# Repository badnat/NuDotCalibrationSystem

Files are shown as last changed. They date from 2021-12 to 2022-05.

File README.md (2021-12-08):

# NuDotCalibrationSystem

This project is for the NuDot Experiment https://jgruszko.web.unc.edu/experiments/. I am a student at UNC who will be graduating in May 2022. I am working with Dr. Gruszko to develop the code and electronics to control the calibration system for the NuDot experiment. The goal of this experiment is to detect neutrinoless double beta decay. Neutrinoless double beta decay is a very rare phenomenon. Because of this, it is difficult to distinguish signal from background during detection. NuDots goal is to reduce the background by detecting cherenkov radiation from single electron events produced by background events as opposed to the double electrons given off by double beta decay. 
 
The goal of my code and electronics is to move a point beta ray source to an exact height, inclination, and rotation. Knowing these allows NuDot to calibrate the precise timings given by the detectors. These timings are extremely important for event building, where we determine details about the event causing the signal such as the position and energy. 

## My Approach and Method
Having previously taken a class full dedicated to working with microcontrollers, my first thought for this project was to use a Raspberry Pi. I ruled out Arduinos because I needed a file system to save multiple files and wanted the flexibility of a microcontroller with an OS for testing purposes. The problem ultimately boils down to moving 3 stepper motors into position, verifying the accuracy of that position, and recording that position for and future movements of the stepper. 
 
I achieved these objectives by using python code to control the stepper motors and a c++ program to read the data from the stepper encoders, interpret the data, and store the position in a file. The python code will only move the stepper and the c++ code will only determine its position. This allows me to independently verify the positions of the steppers and compensate for any step skipping that might occur. This ensures that we always accurately know the positions of the steppers which is important for both calibration and mechanical reasons. Obviously we need to accurately know the position of the beta source to calibrate the system, but there are also a few mechanical hard stops that the steppers would be unable to push past (blocked by a lot of metal). I could have used a sensor to determine the position in space but decided to make my code very robust to avoid the issue all together. 

#### Code Structure
I decided on an object oriented approach for ease of use and abstraction. The [Calibrator](https://github.com/badnat/NuDotCalibrationSystem/blob/main/calibrator.py) object is primarily for abstraction and handling error handling/edge cases. It holds all of the [Stepper](https://github.com/badnat/NuDotCalibrationSystem/blob/main/stepper.py) objects which send the signals to the stepper motors to move them. The [Stepper](https://github.com/badnat/NuDotCalibrationSystem/blob/main/stepper.py) objects also use bash commands to start up the [encoder](https://github.com/badnat/NuDotCalibrationSystem/blob/main/encoder.cpp) code for that stepper motor. 

## Assembled Calibration System
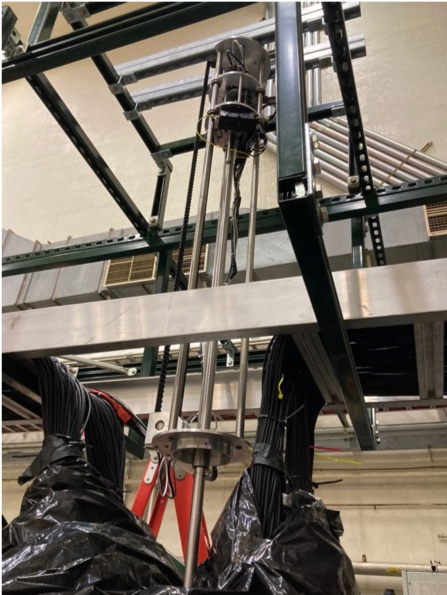
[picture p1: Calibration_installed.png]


## Challenges and Future Improvements
- Fully implementation of code and handling a few more edge cases (almost finished)
- Implement code for the Daq system to control the Rpi remotely using ssh keys
- Finalize Electronics using a custom PCB and CAT6 cable to send signals to the steppers and to the Pi from the encoders

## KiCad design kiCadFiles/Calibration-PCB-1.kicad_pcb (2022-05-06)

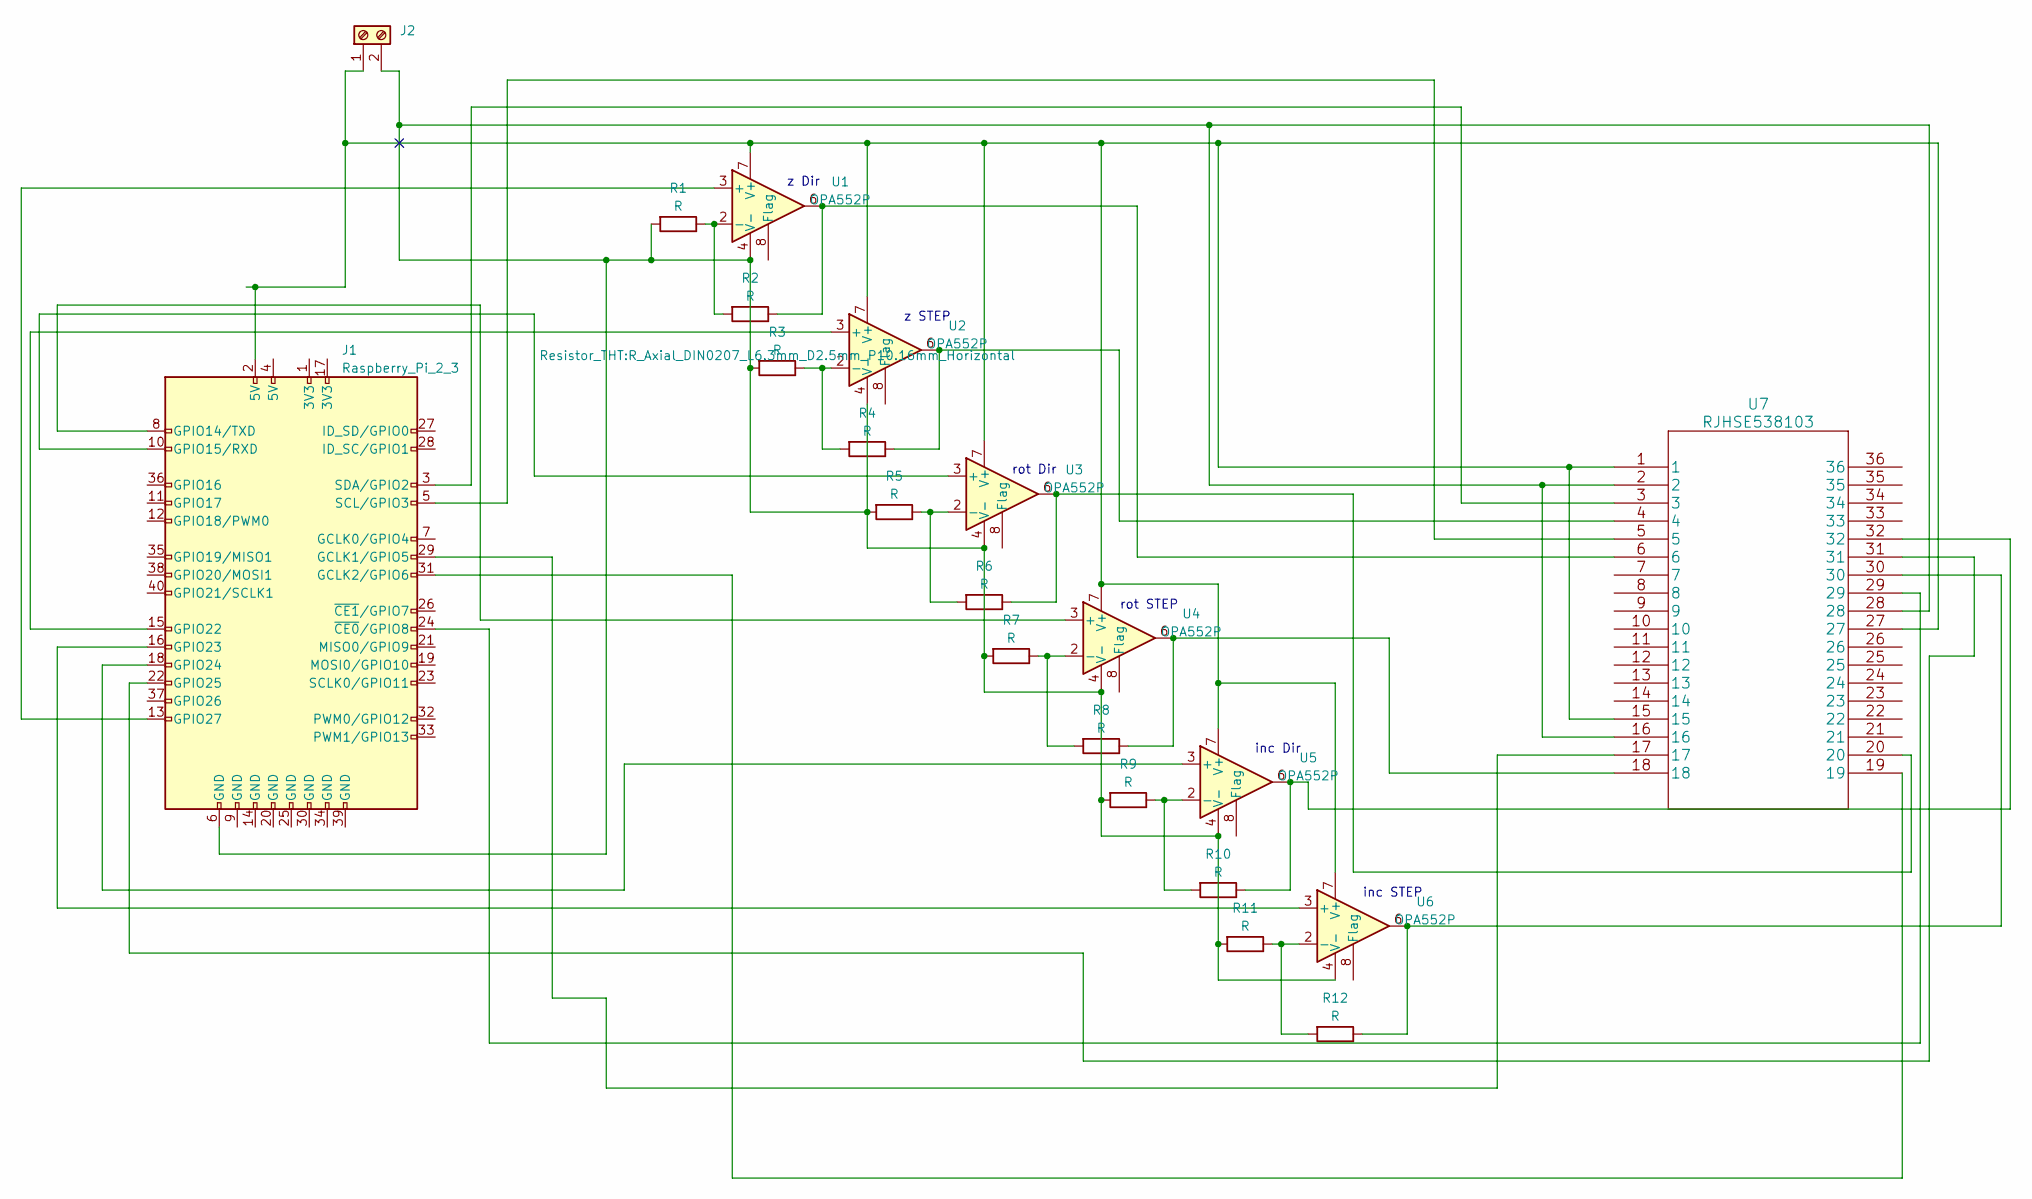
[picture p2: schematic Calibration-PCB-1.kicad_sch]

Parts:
J1: Raspberry_Pi_2_3; PinHeader_2x20_P2.54mm_Vertical
J2: (no value)
R1, R2, R3, R4, R5, R6, R7, R8, R9, R10, R11, R12: R; R_Axial_DIN0207_L6.3mm_D2.5mm_P10.16mm_Horizontal
U1, U2, U3, U4, U5, U6: OPA552P; DIP-8_W7.62mm
U7: RJHSE538103

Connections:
unnamed: J1.2 (5V), J2.1, U1.7 (V+), U2.7 (V+), U3.7 (V+), U4.7 (V+), U5.7 (V+), U6.7 (V+), U7.1, U7.15, U7.27
unnamed: J1.29 (GCLK1/GPIO5), U7.17
unnamed: J1.31 (GCLK2/GPIO6), U7.19
unnamed: J1.6 (GND), J2.2, R1.2, R3.2, R5.2, R7.2, R9.2, R11.2, U1.4 (V-), U2.4 (V-), U3.4 (V-), U4.4 (V-), U5.4 (V-), U6.4 (V-), U7.2, U7.16, U7.28
unnamed: J1.13 (GPIO27), U1.3 (+)
unnamed: J1.5 (SCL/GPIO3), U7.5
unnamed: J1.3 (SDA/GPIO2), U7.3
unnamed: R2.1, U1.6, U7.6
unnamed: R4.1, U2.6, U7.4
unnamed: R6.1, U3.6, U7.20
unnamed: R8.1, U4.6, U7.18
unnamed: R1.1, R2.2, U1.2 (-)
unnamed: J1.15 (GPIO22), U2.3 (+)
unnamed: R3.1, R4.2, U2.2 (-)
unnamed: J1.10 (GPIO15/RXD), U3.3 (+)
unnamed: R5.1, R6.2, U3.2 (-)
unnamed: J1.8 (GPIO14/TXD), U4.3 (+)
unnamed: R7.1, R8.2, U4.2 (-)
unnamed: J1.18 (GPIO24), U5.3 (+)
unnamed: R9.1, R10.2, U5.2 (-)
unnamed: J1.16 (GPIO23), U6.3 (+)
unnamed: R11.1, R12.2, U6.2 (-)
unnamed: J1.24 (~CE0/GPIO8), U7.29
unnamed: R12.1, U6.6, U7.30
unnamed: J1.22 (GPIO25), U7.31
unnamed: R10.1, U5.6, U7.32

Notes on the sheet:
rot STEP
rot Dir
z STEP
inc Dir
inc STEP
z Dir

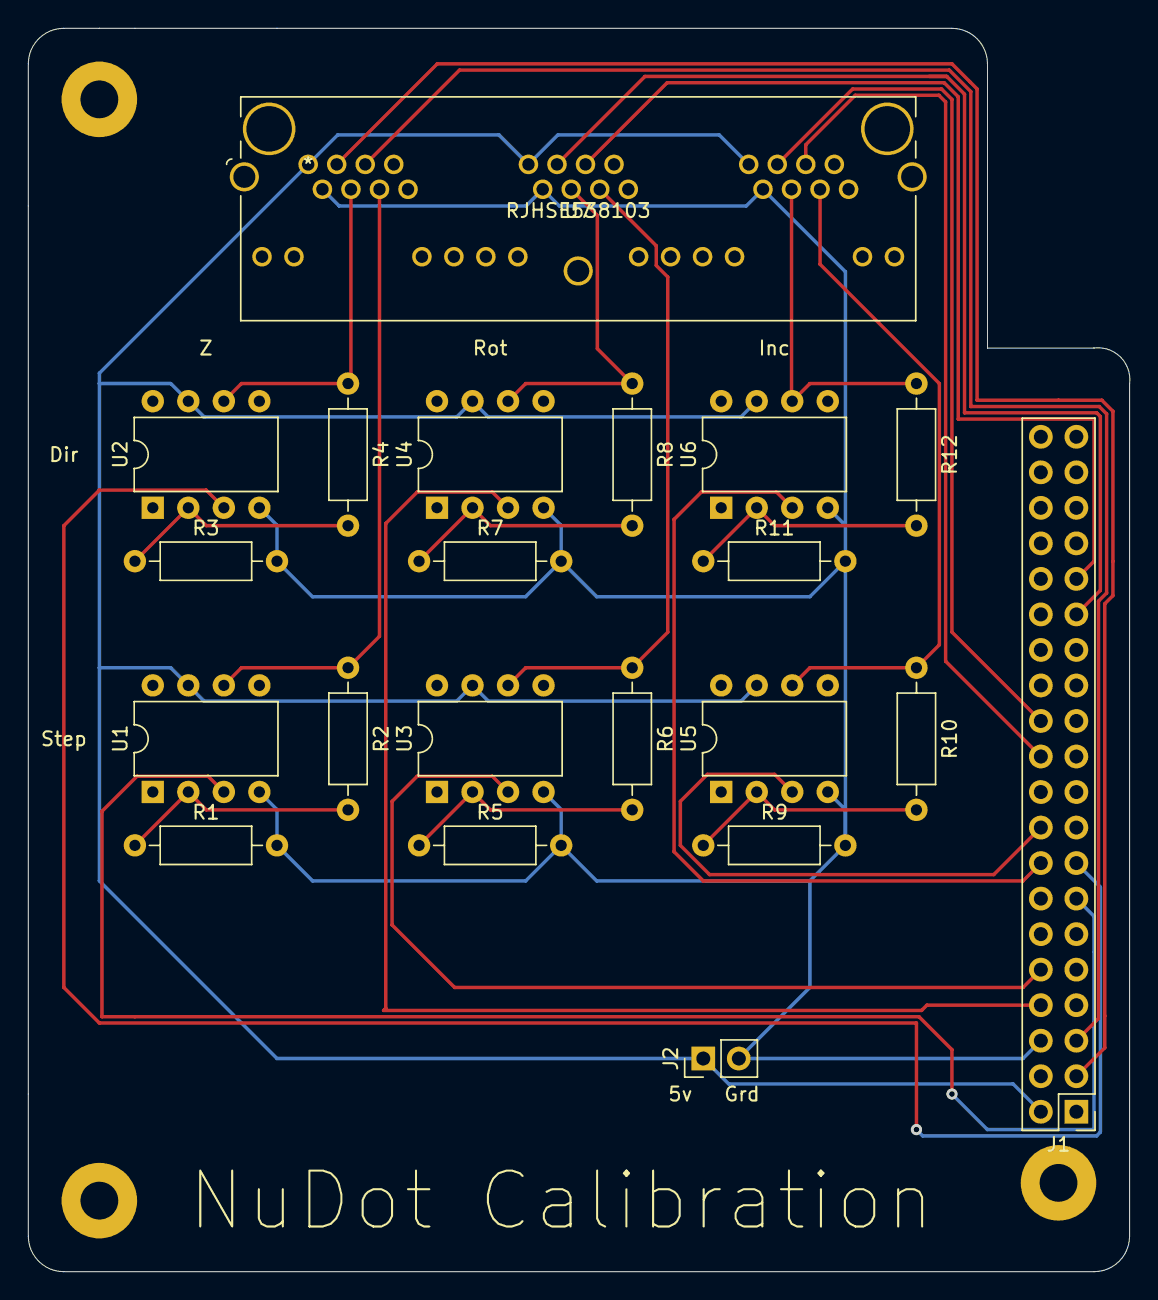
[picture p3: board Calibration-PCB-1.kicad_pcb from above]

Board: 2 copper layers, 78.8 x 88.9 mm, 21 parts (0 on the bottom side), 26 nets.

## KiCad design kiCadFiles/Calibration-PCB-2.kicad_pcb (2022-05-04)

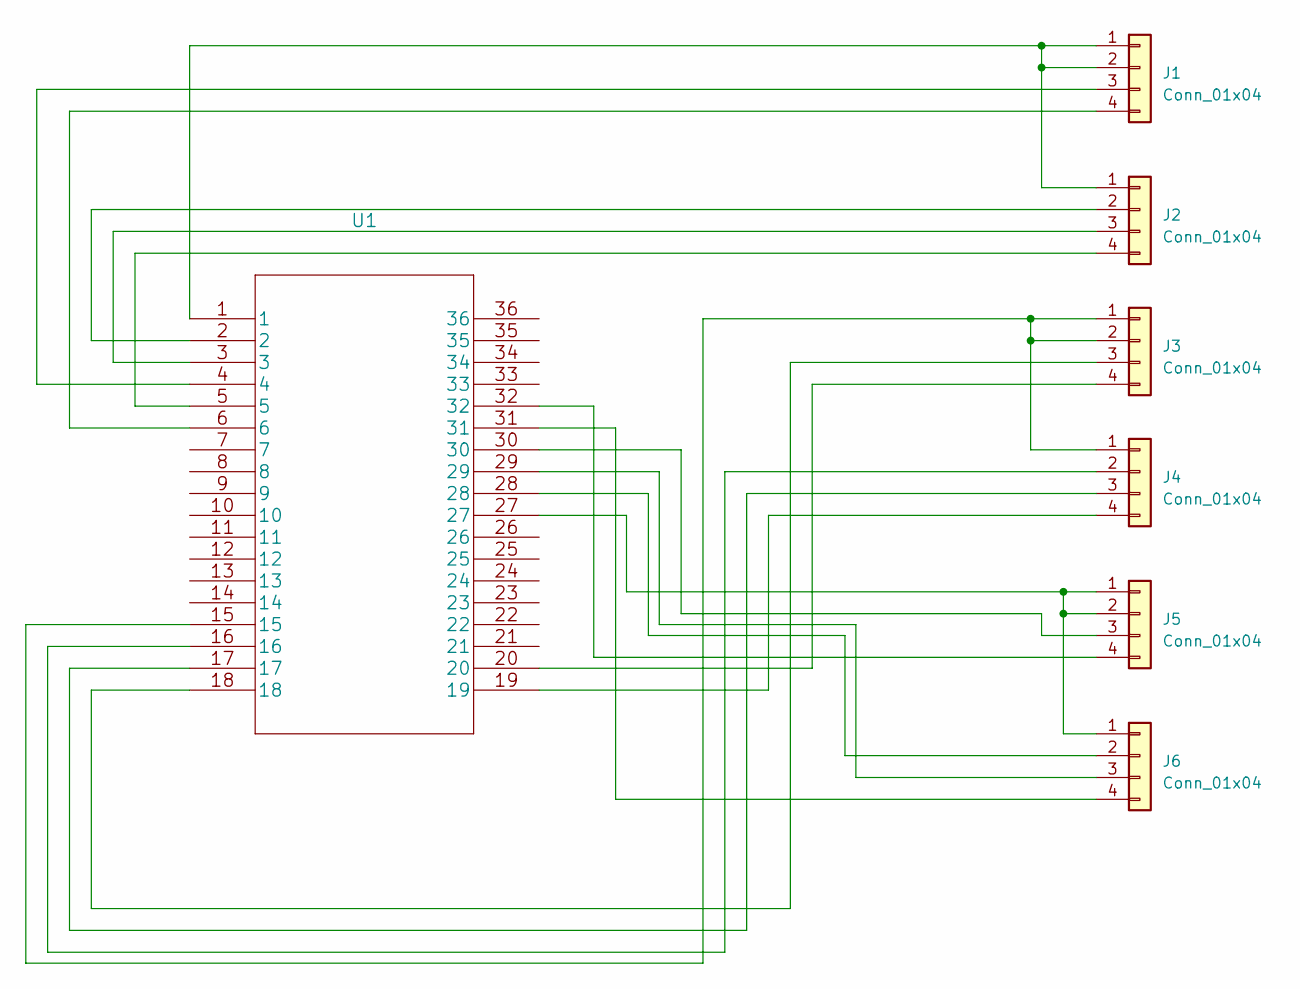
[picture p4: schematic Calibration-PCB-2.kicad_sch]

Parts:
J1, J2, J3, J4, J5, J6: Conn_01x04; PinSocket_1x04_P2.54mm_Vertical
U1: (no value)

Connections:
unnamed: J1.1, J1.2, J2.1, U1.1
unnamed: J1.3, U1.4
unnamed: J1.4, U1.6
unnamed: J2.2, U1.2
unnamed: J2.3, U1.3
unnamed: J2.4, U1.5
unnamed: J3.1, J3.2, J4.1, U1.15
unnamed: J3.3, U1.18
unnamed: J3.4, U1.20
unnamed: J4.2, U1.16
unnamed: J4.3, U1.17
unnamed: J4.4, U1.19
unnamed: J5.1, J5.2, J6.1, U1.27
unnamed: J5.3, U1.30
unnamed: J5.4, U1.32
unnamed: J6.2, U1.28
unnamed: J6.3, U1.29
unnamed: J6.4, U1.31

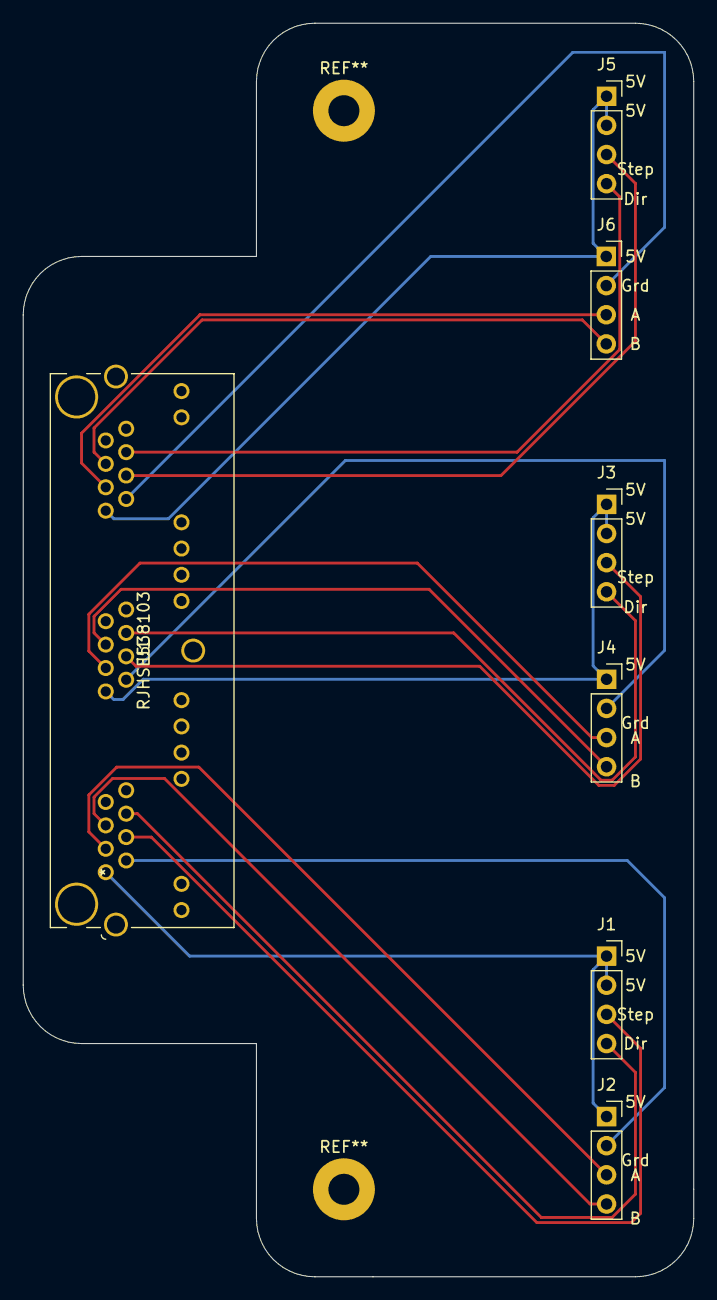
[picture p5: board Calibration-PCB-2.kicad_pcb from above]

Board: 2 copper layers, 58.4 x 109.2 mm, 7 parts (0 on the bottom side), 18 nets.

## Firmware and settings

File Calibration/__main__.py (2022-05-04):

import sys
from stepper import Stepper
from calibrator import Calibrator

# step and dir are pin numbers
# A and B are GPIO numbers

zPW = 5000
zDir = 15
zStep = 13
# angle upper and lower bound
zLower = 0
zUpper = 5730
zA = 2
zB = 3

rotPW = 5000
rotDir = 10
rotStep = 8
# angle upper and lower bound
rotLower = -180
rotUpper = 180
rotA = 5
rotB = 6


incPW = 5000
incDir = 16
incStep = 18
# angle upper and lower bound
incLower = -90
incUpper = 90
incA = 8
incB = 25

# returns a tuple of floats 
# z (in meters), rot (in degrees), inc (in degrees)
def readCoords():
    args = sys.argv[1:]
    return (float(args[0]), float(args[1]), float(args[2]))


def main():
    try:
        zDist, rotAng, incAng = readCoords()
    except IndexError:
        print("please enter params: <z distance in meters> <rotation angle in degrees> <inclination angle in degrees>")
        return
        
    zStepper = Stepper(zPW, "z", zDir, zStep, zLower, zUpper, zA, zB)
    rotStepper = Stepper(rotPW, "rot", rotDir, rotStep, rotLower, rotUpper, rotA, rotB)
    incStepper = Stepper(incPW, "inc", incDir, incStep, incLower, incUpper, incA, incB)
    cal = Calibrator(zStepper, rotStepper, incStepper)
    zAng = cal.distanceToAngle(zDist, 1e-2)
    cal.calibrate(zAng, rotAng, incAng)

if __name__ == "__main__":
    main()

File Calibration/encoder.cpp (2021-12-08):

#include <iostream>
#include <pigpio.h>
#include <bits/stdc++.h>
#include <fstream>
using namespace std; 

class Encoder {
    private:
    int A;
    int B;
    char* name;
    double angle = 0.0;

    int wasA = 0;
    int isA = 0;
    int count = 0;
    int isB = 0;

    int d = 0;      // counts how many times listener doesn't get an edge

    public:
    Encoder(int A, int B, char* name) {
        gpioInitialise();

        this->A = A;
        this->B = B;
        this->name = name;

        ifstream fin(name);
        fin >> this->angle;

        gpioSetMode(A, PI_INPUT);
        gpioSetMode(B, PI_INPUT);
        gpioWrite(A, 0);
        gpioWrite(B, 0);

        wasA = gpioRead(A);
    }

    public:
    void listen() {
        int dir;
        while (d < 100000 || count < 3) {
            isB = gpioRead(B);
            isA = gpioRead(A);
            if(!wasA && isA) {
                d = 0;
                count++;
                if (count == 2) {
                    dir = isB;
                }
            } else {
                d++;
            }
            wasA = isA;
        }
        if (dir) {
            angle = angle - (round((count) / 5.0) * 1.8);
        } else {
            angle = angle + (round((count) / 5.0) * 1.8);
        }
        ofstream file;
        file.open(name);
        file << angle;
        file.close();
        cout << "ENCODER : " << name << " current angle = " << angle << " with " << round((count) / 5.0) << " steps" << endl;
    }
};

int myAtoi(char* str) {
    int result = 0;
    for (int i = 0; str[i] != '\0'; i++) {
        result = result * 10 + str[i] - '0';
    }
    return result;
}

int main(int argv, char** argc) {
    int A;
    int B;
    char* name;

    A = myAtoi(argc[1]);
    B = myAtoi(argc[2]);
    name = argc[3];

    Encoder *ptr = new Encoder(A, B, name);
    Encoder e = *ptr;
    e.listen();
    gpioWrite(A, 0);
    gpioWrite(B, 0);
    return 0;
}

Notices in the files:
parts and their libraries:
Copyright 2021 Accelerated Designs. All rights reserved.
